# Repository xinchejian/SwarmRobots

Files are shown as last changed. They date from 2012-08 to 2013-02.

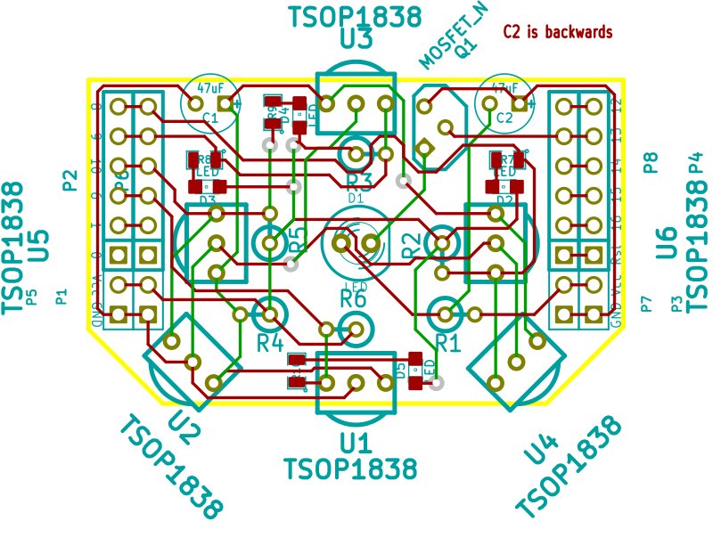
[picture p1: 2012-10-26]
AtTiny2313/hardware/swarmIRShield/swarmIR-brd.jpg

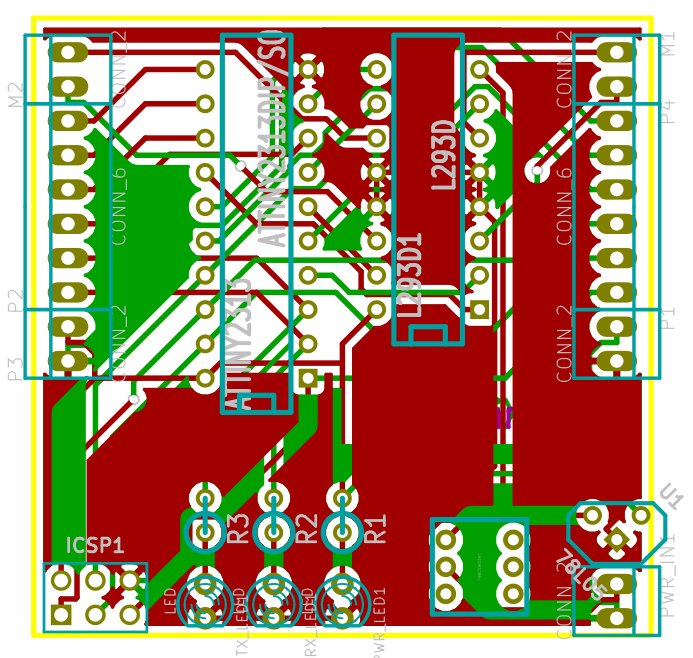
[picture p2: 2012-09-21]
AtTiny2313/hardware/mainPCB/swarmrobot-brd.jpg

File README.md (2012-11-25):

xcj_swarm
=========

Xinchejian Swarm Robot project

Introduction:

Build a swarm of robots with autonomus behavior to achieve their goals by interacting with each other using IR communication.

See each xinCheJian wiki for assembly instructions and information.

Original Requirements:
  Each basic robot contains the following:
	- 1x microcontroller Attiny2313
	- 1x motor controller L293D
	- 2x gear motors
	- 1x LiPo battery 3.7V
	Sensor shield

A custom made PCB will be used. This PCB will be mounted into a 3D printed casing which contains the gear motors and the wheels as well the IR sensor array.

Goal is that the maximum price for the basic robot should not exceed 5US$ (without shield)

Each robot will have a basic programming and basic hardware platform. 
The basic programming is:
1. Self protection: 
	- check your battery status
	- find the charging station when battery runs low
	- avoid obstacles and other robots
	- search for power (sunlight etc.)
2. Community (swarm) needs:
	- search for building material
	- search for dead robots
	- bring dead robots to the charging station
	- help dead robots with a charger robot
	- tell others where to find power (sunlight)
	- tell others where is an obstacle or danger

Folder structure:
	/32u4-edwardrf	work in progress - check XCJ mailing list for later versions.
	/AtTiny2313	AtTiny2313 version - that won the AFRON competition
	/ATMEGA328	version based on 
	/ATMEGA168	latest super version (replaces UNO version).

	Note there is a LARGE amount of direct compatability between the code for ALL versions. Differences to note are:
		- different IO pins - see "Arduino, AtTiny, L293 and header pin mappings.ods"
		- size of memory limits size of code
		- AtTiny versions have fewer IO commands available. See http://wiki.xinchejian.com/wiki/Programming-AFRON

Branches & master
	- Please use branches to do YOUR work before committing back to the master!
	- Goal is for the master to be 'production ready' at ALL TIMES!

More at the XinCheJian website wiki.xinchejian.com 
	- the original Swarmrobot pages at http://wiki.xinchejian.com/wiki/Swarm_robots
	- collated summary and AFRON competition entry
	http://wiki.xinchejian.com/wiki/Category:AFRON_$10_Robot_Competition

	latest Swarmrobot index - entry page is now: http://wiki.xinchejian.com/wiki/Category:Swarm_Robots

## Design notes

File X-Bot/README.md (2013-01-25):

简介：
   X-Bot是一款群体机器人（Swarm Robot），让这样一群小巧的机器人来实现蚁群可以完成的任务，这就是群体机器人。它由来自新车间（xinchejian.com）创客空间成员组建的一个小组创建。该机器人是基于红外线传感而制作的，它的特点是低成本、易于实践和多功能。该机器人初级版在2012年9月 “AFRON $10 robot challenge” 上获得常规组的第二名。
   该项目有Lutz提议建立，于2012年4月启动，其目的是让成员通过实践可以学到多样的技能，并促进人之间的交流。该目的通过构建个体功能很简单，但通过它们之间的合作可以完成复杂任务的小机器人来实现，这就是Swarm Robot。
该项目在进行中，核心成员为：
   Lutz Michaelis： 德国 （发起人）
   Spencer F：澳大利亚
   Edward Jiang： 中国
   Sunny Sun ：中国
   Leo Yan ： 中国

   在这里归档是LeoYan在其基础上的进一步发展的中级版本，采用了ATMEGA328，拥有更大的创作空间，通过您的加入将会使其功能更完善，也将形成一个圈子，一起交流，一起make stuff。

版权声明：
    所有文档和硬件设计采用：CC BY-NC 3.0 CN ， see <http://creativecommons.net.cn/licenses>
    所有软件代码采用      ：GPL3.0 ，          see <http://www.gnu.org/licenses/>

# English

## Programming

* Checkout and compile the log
 * Set target to Arduino Uno
 * symlink source to SwarmRobot (required by Arduino IDE projects)
* Charge the X-Bot fully
* Configure your X-Bot ID in Swbot.Config.h
 * If you want to start _START_REMOTE_CONTROL
 * Select the behavior you want

```
  #define ROBOT_TYPE_ANT  0x10 (food hunter)
  #define ROBOT_TYPE_ANT_LINEUP 0x11 (line up to and follow the higher id)
  #define ROBOT_TYPE_FOOD 0x21 (turns your X-Bot into a edible source of food)
```
 * Verify the program (compilation step)
* Connect the USB TTL Programmer v2 to your USB
 * Align VCC to VCC
* Upload, should end up with Arduino 1.0.1:

```
avrdude done.  Thank you.
```

## Details

## Behavior changes

In Action.cpp, behavior is defined in RuleTbl as a state machine.

Below, an example using the food hunter behavior:

This represents the current state and the action to do (internal state):

    {INTERIORINFO, TASK_STAGE, TS_LOOKING,  0, 0, 0,  true},

The action is activated under each state by ANYINFO:

    {ANYINFO, 0, 0,  ACTION_IN_SET, TASK_STAGE, TS_LOOKING,  false },

(last boolean is used to create a linked-list of actions to be done following a state)

The first 3 parameters define the conditional for an action... In the case of ANYINFO, there's no conditional so parameters are zero:

    {ANYINFO, 0, 0,  ACTION_EXT_LED, LED_MODE_MANUAL, 0B00,  true},

If the type of message is FOOD, the action is to set the internal variable target to true and keep target id

    {ROBOTINFO_TYPE, ROBOT_ID_ANY, ROBOT_TYPE_FOOD,  ACTION_IN_SET, TARGET, INFO_STATE_SET,  true},

If the TARGET variable is set, then change the state to TS_FOUND:

    {INTERIORINFO, TARGET, INFO_STATE_SET,  ACTION_IN_SET, TASK_STAGE, TS_FOUND,  false},

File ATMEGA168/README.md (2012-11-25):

xcj_swarm
=========

Xinchejian Swarm Robot project

This folder is for the Arduino atmega168 based SwarmRobot version.

It is the most advanced hardware and software SwarmRobot as at November 2012!

Folder structure:
	/hardware	- Eagle v6 schematic and PCB files
	/source 	- all the source code - can edit/compile in Arduino GUI!

Contact: leo.yan.cn@gmail.com

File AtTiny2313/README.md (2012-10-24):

xcj_swarm/AtTiny2313
=========

Part of Xinchejian Swarm Robot project - contains ALL software and hardware for AtTiny2313 SwarmRobots.

As there are now many different types of SwarmRobots, moving all AtTiny2313 files here.

hardware/swarmIRShield			Shield for IR follow/avoid, object detection and communications
hardware/mainPCB			Main processor & motor controller

software/IR_Follow			IR follow has bugs not working very well
software/IR_Follow_AFRON		IR follow released for AFRON competition + has bug fix
software/IR_object_detection		IR object detection
software/SwitchShield_Avoid_Follow  	Wall avoid or follow using micro-switch shield (only on proto-board - no PCB done yet!)
/software/SwarmIRControl		SwarmRobot(s) respond to RC5 IR comamnds
					Build from command line 'make' - so you need a compiler setup!
/software/SwarmIRControllerArduino	Send RC5 commands to SwarmRobot(s) using an Arduino 
						(most remotes in China are NEC protocol!)
/software/Swarm_Random_Demo		SwarmRobot moves in random direction for random time (6 seconds max) 
						- no shield required!

... to do for software/SwarmIRControl
	- add non-rc5 ie any IR follow to SwarmIRControl
	- more doco on compiling & settting up compiler....
		(if you have Arduino installed - you should have it already, maybe need path..)

************************************************************
Changes made to move from previous mess to this structure:-

/swarmIR		-> AtTiny2313/hardware/swarmIRShield
/kicad			-> AtTiny2313/hardware/mainPCB

/source-Avoid-Follow	-> AtTiny2313/software/SwitchShield_Avoid_Follow 
/source-IR		-> AtTiny2313/software/IR_Follow_AFRON
/swarm_wall_follow_ir	-> AtTiny2313/software/IR_object_detection

All the Arduino code files also renamed so can open sketches in the folder!

************************************************************

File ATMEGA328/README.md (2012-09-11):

xcj_swarm
=========

Xinchejian Swarm Robot project

This folder is for the custom PCB ATMEGA328 SwarmRobot version.

Folder structure:

	/eagle 		kicad schematics and PCB design files
	/source		source code

	Note there is a LARGE amount of direct compatability between the code for ALL versions. Differences to note are:
		- different IO pins - see "Arduino, AtTiny, L293 and header pin mappings.ods"
		- size of memory limits size of code
		- AtTiny versions have fewer IO commands available. See http://wiki.xinchejian.com/wiki/Programming-AFRON

More at the XinCheJian website wiki.xinchejian.com 
	- the original Swarmrobot pages at http://wiki.xinchejian.com/wiki/Swarm_robots
	- collated summary and AFRON competition entry
		 - URL not yet published, but after 15/9/2012 you will find it via 
				http://wiki.xinchejian.com/wiki/Category:AFRON_$10_Robot_Competition

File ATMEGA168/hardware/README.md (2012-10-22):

xcj_swarm
=========

Xinchejian Swarm Robot project

Introduction:

Build a swarm of robots with autonomus behavior to achieve their goals by interacting with each other using IR communication.

Requirements:

Each basic robot contains the following:
	
	- 1x microcontroller Attiny2313
	- 1x motor controller L293D
	- 2x gear motors
	- 1x LiPo battery 3.7V
	Sensor shield

A custom made PCB will be used. This PCB will be mounted into a 3D printed casing which contains the gear motors and the wheels as well the IR sensor array.

Goal is that the maximum price for the basic robot should not exceed 5US$ (without shield)

Each robot will have a basic programming and basic hardware platform. 
The basic programming is:

1. Self protection: 
	- check your battery status
	- find the charging station when battery runs low
	- avoid obstacles and other robots
	- search for power (sunlight etc.)
2. Community (swarm) needs:
	- search for building material
	- search for dead robots
	- bring dead robots to the charging station
	- help dead robots with a charger robot
	- tell others where to find power (sunlight)
	- tell others where is an obstacle or danger

Folder structure:

	/kicad 		AtTin2313 - kicad schematics and PCB design files
	/source		AtTin2313 - source code

	/ATMEGA328	version based on 
	/UNO		version built onto and existing Arduino UNO.

	Note there is a LARGE amount of direct compatability between the code for ALL versions. Differences to note are:
		- different IO pins - see "Arduino, AtTiny, L293 and header pin mappings.ods"
		- size of memory limits size of code
		- AtTiny versions have fewer IO commands available. See http://wiki.xinchejian.com/wiki/Programming-AFRON

Branches & master
	- Please use branches to do YOUR work before committing back to the master!
	- Goal is for the master to be 'production ready' at ALL TIMES!

Sample Git info:
    http://kentnguyen.com/development/visualized-git-practices-for-team/
    http://gitref.org/branching/
    http://marklodato.github.com/visual-git-guide/index-en.html
    http://think-like-a-git.net/
    https://github.com/diaspora/diaspora/wiki/Git-Workflow

More at the XinCheJian website wiki.xinchejian.com 
	- the original Swarmrobot pages at http://wiki.xinchejian.com/wiki/Swarm_robots
	- collated summary and AFRON competition entry
		 - URL not yet published, but after 15/9/2012 you will find it via 
				http://wiki.xinchejian.com/wiki/Category:AFRON_$10_Robot_Competition

************************************************************
Changes made to move from previous mess to this structure:-

/swarmIR		-> AtTiny2313/hardware/swarmIRShield
/kicad			-> AtTiny2313/hardware/mainPCB

/source-Avoid-Follow	-> AtTiny2313/software/SwitchShield_Avoid_Follow 
/source-IR		-> AtTiny2313/software/IR_Follow_AFRON
/swarm_wall_follow_ir	-> AtTiny2313/software/IR_object_detection

All the Arduino code files also renamed so can open sketches in the folder!

************************************************************

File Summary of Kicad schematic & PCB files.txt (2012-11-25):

2012-11-25 This file is now just for historical use - it now lenger matches current structure!

The following is a history of Schematic & PCB files, extracted from the git commit log.

5/6/12   swarmrobot 			- Schematic & PCB

6/6/12   swarmrobot_new			- PCB ** 9/8/12 Edward & Lutz confirmed this was THE PCB that was made AND is the CURRENT PCB.
6/6/12   swarmrobot_new_route 		- routing only? (.do, dsn, log, rtr, ses, sts)

20/6/12  swarmrobot_new_reduced 	- Schematic & PCB (pdf, jpg copies added 8/8/12)
20/6/12  attiny85_board_optimized 	- PCB

?? Uncommited work in progress to reduce PCB size.

10/8/12	kicad/edward_version/swarmrobot.* edward's version of routed prototype sent for printing
			attiny85_board_optimized.*
			swarmrobot_new_route.*
			swarmrobot_new_reduced.*
			swarmrobot.*				<< Looks complete & seems to match actual PCBs made!

			/export9Aug2012
				swarmrobot.*

			/export14jul
				swarmrobot.*

			/lib

11/9/12 big tidy up prior to AFRON competition!
	- deleted all files from /kicad & commited
	- moved kicad/edward_version/swarmrobot.* & /export9Aug2012 to /kicad
	- deleted all remaining files in kicad/edward_version/
	- committed		-- if you need any of the older files, please go to the commits tab and find them!
						or try a visiual git interface like gitk
						or read something like http://rogerdudler.github.com/git-guide/

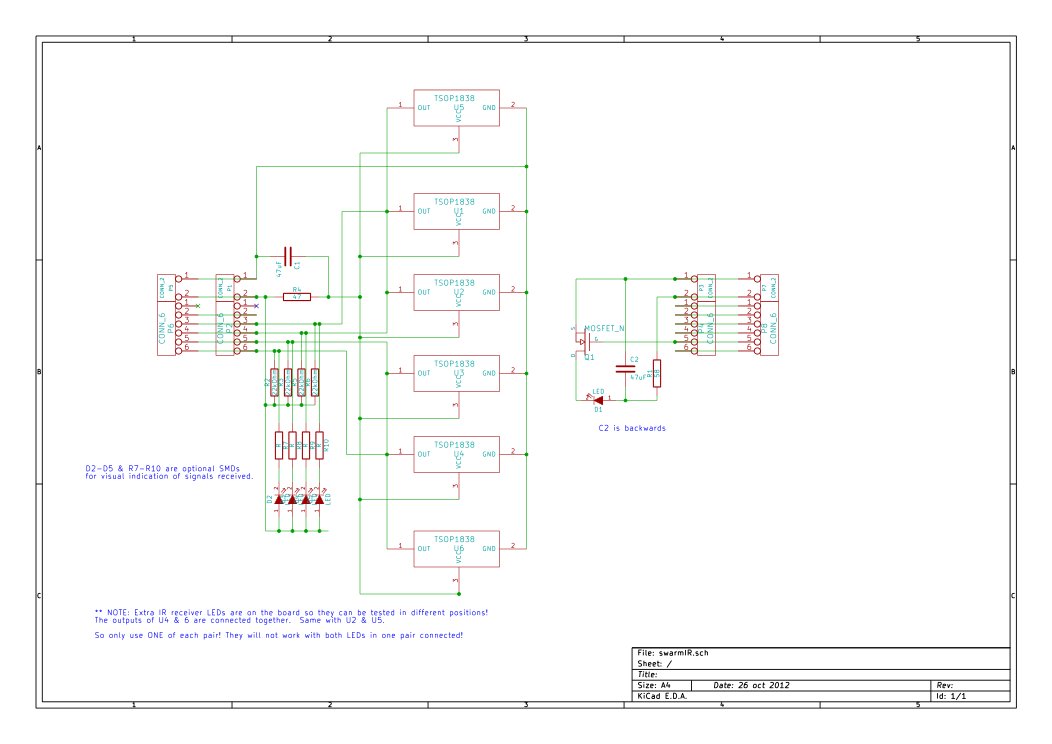
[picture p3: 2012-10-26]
AtTiny2313/hardware/swarmIRShield/swarmIR.jpg

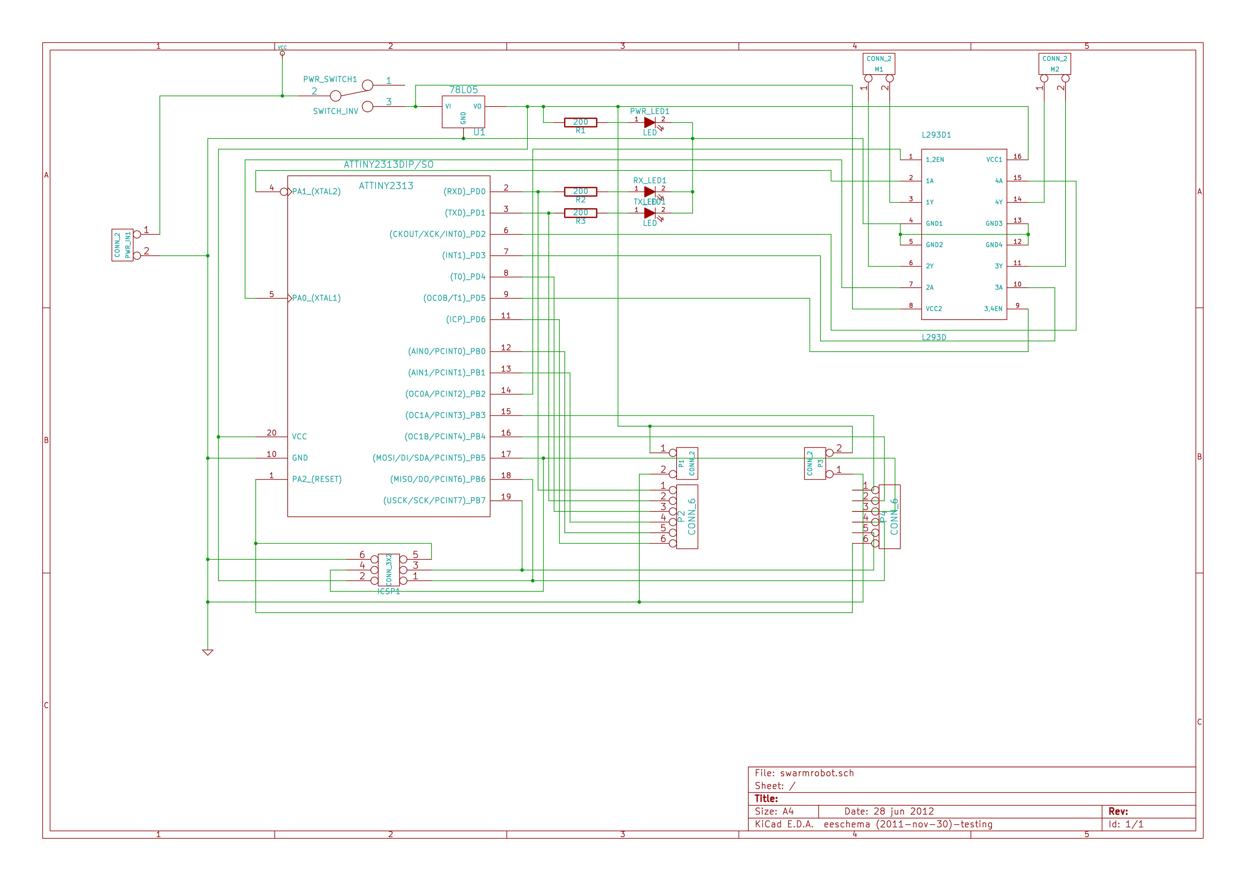
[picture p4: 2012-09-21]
AtTiny2313/hardware/mainPCB/swarmrobot.jpg

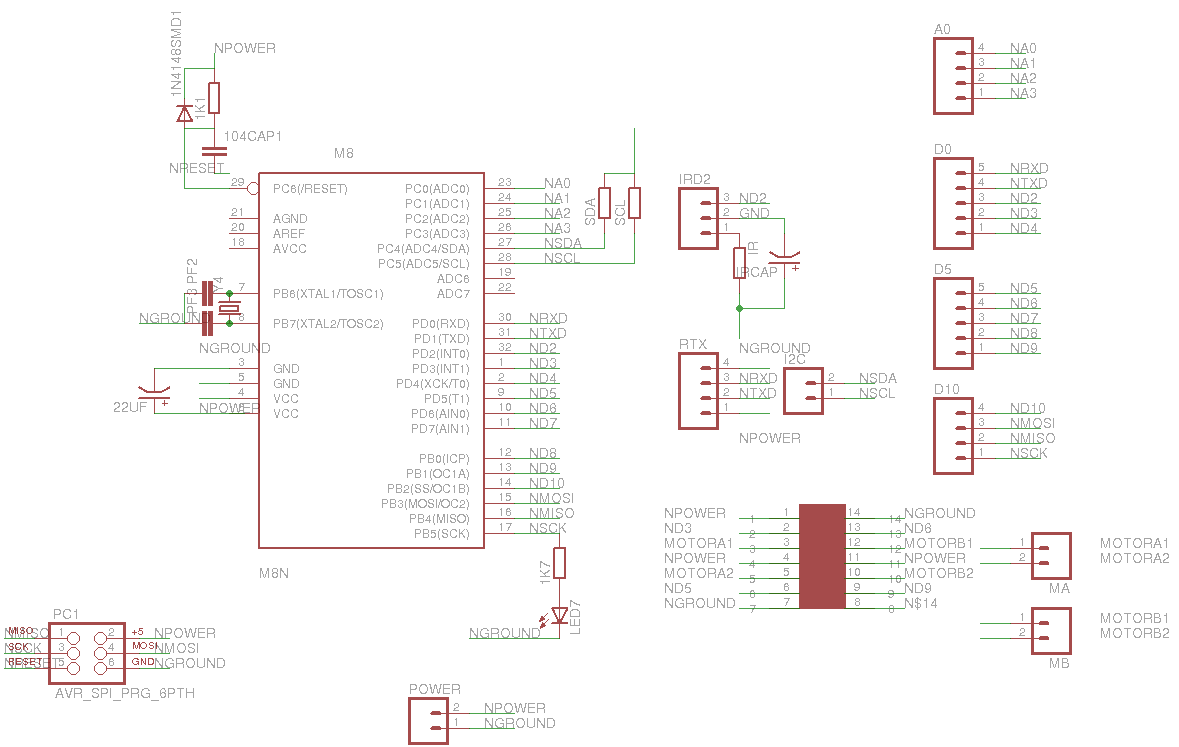
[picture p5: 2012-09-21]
ATMEGA328/eagle/pcbmotor_schematic.png

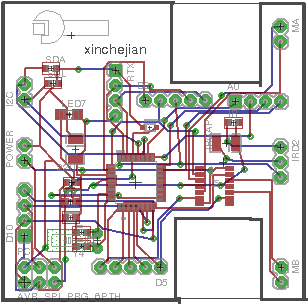
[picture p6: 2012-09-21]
ATMEGA328/eagle/pcbmotor.png

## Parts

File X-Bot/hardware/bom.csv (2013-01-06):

名称 | Item | Package | Type | Quantity
MCU | MCU | TQFP | ATMEGA328P-AU | 1
电机驱动 | MOTOR DRIVER | MFP14S | LB1836M | 1
晶振 | CRISTAL | EIA3528 (TXC-7A) | 16M | 1
大电流磁珠 | Ferrite bead | 0805 | 大电流磁珠 300R 1.5A | 2
红外发射管 | IR-LED | 5mm | IR-LED | 1
一体化红外接收管 | IR-RECEIVER | TSOP | NJL21V400A | 4
LED | LED | 0805 | green | 2
LED | LED | 0805 | orange | 4
LED | LED | 5mm | red LED 红色 | 1
排针 | Pin header | 间距2.54mm 针长12mm | 1X40 | 0.5
排针 | Pin header | 间距2.54mm 针长12mm | 2X40 | 0.1
排针 | Pin header | 间距2.54mm | 90度 1X40 | 0.2
排母 | Pin socket | 2.54mm | 1X08 | 3
排母 | Pin socket | 2.54mm | 1X12 | 2
电阻 | resistor | 0805 | 100K (1/100precision) | 1
电阻 | resistor | 0805 | 33K (1/100precision) | 1
电阻 | resistor | 0805 | 1k | 7
电阻 | resistor | 0805 | 150R | 2
电阻 | resistor | 0805 | 10K | 1
电阻 | resistor | 0805 | 47R | 4
瓷电容 | capacitor | 0805 | 0.1uF | 6
瓷电容 | capacitor | 0805 | 22p | 2
瓷电容 | capacitor | 1206 | 22uF | 5
钽电容 | tantalum capacitor | EIA3528 | 47uF | 1
带保护板锂电池 | Li Battery | Larger than 180mA | 3cmX2cm | 1
小拨动开关 | 小拨动开关 | 8mm*4mm 柄5mm | SS-12D0 | 1
Motor 微型直流减速电机 | Motor 微型直流减速电机 |  | J9xx | 2
Screw 平头螺丝 | Screw 平头螺丝 |  | M2*8 | 2
wheel 皮带轮 | wheel 皮带轮 | 橙色或白色 | 17*4*1.9 | 2
垫片 | 垫片 | O型 | inter diameter 2.5 mm | 2
O型圈密封圈 | O型圈密封圈 |  | 外径15，线径2 | 2
硬纸片 | Card board | 30mmX30mm | 比如牙膏包装盒，不透光 | 1

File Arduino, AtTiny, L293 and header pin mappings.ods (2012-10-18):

Arduino | Atmega328-P | Atmega328-AU | Attiny2313 |  |  |  |  | PCB – 30 sent to make on 2012-08-9
IO Pin# | Chip pin# | Chip pin# | pin | Use1 | Use2 | Use3 | Pin | Use 1 | Use 2
RESET | 1 | 29 | 1 | PA2 | /Reset | dW | P4 1 |  | ICSP5 Reset
D0 | 2 | 30 | 2 | PD0 | RXD |  | P2 1 | Rx
D1 | 3 | 31 | 3 | PD1 | TXD |  | P2 2 | Tx |  | L293D (care dif pinouts??)
D2 | 4 | 32 | 4 | PA1 | XTAL2 |  |  | MLF |  | 2 | In1
D3 | 5 | 1 | 5 | PA0 | XTAL1 |  |  | MLB |  | 7 | In2
D4 | 6 | 2 | 6 | PD2 | CKOUT/XCK | INT0 |  | MRF |  | 15 | In4
D5 | 11 | 9 | 7 | PD3 |  | INT1 |  | MRB |  | 10 | In3
D6 | 12 | 10 | 8 | PD4 |  | T0 | P2 3 | IR_FC
D7 | 13 | 11 | 9 | PD5 | OSCOB | T1 |  | MREn |  | 9 | En2
 |  |  | 10 | GND |  |  |  |  | ICSP6 Gnd
D8 | 14 | 12 | 11 | PD6 | ICP |  | P2 6 | IR_FL
D9 | 15 | 13 | 12 | PB0 | AIN0 | PCINT0 | P2 5 | IR_R
D10 | 16 | 14 | 13 | PB1 | AIN1 | PCINT1 | P2 4 | IR_FR
D11 | 17 | 15 | 14 | PB2 | OCOA | PCINT2 |  | MLEn |  | 1 | En1
D12 | 18 | 16 | 15 | PB3 | OC1A | PCINT3 | P4 6
D13 | 19 | 17 | 16 | PB4 | OC1B | PCINT4 | P4 5 | IR Transmit control
D14 | nc | nc | 17 | PB5 | MOSI/DI/SDA | PCINT5 | P4 4 |  | ICSP4 MOSI
D15 | nc | nc | 18 | PB6 | MISO/DO | PCINT6 | P4 3 |  | ICSP1 MISO
D16 | nc | nc | 19 | PB7 | UCSK/SCL | PCINT7 | P4 2 |  | ICSP3 UCSK or SCL?
 | nc | nc | 20 | VCC |  |  |  |  | ICSP2 Vcc
A0 | 23 | 23 | nc
A1 | 24 | 24 | nc
A2 | 25 | 25 | nc
A3 | 26 | 26 | nc
A4 | 27 | 27 | nc |  |  |  |  |  |  | This document is a work in progress – please help verify & comment on it's accuracy!
A5 | 28 | 28 | nc
A6 | nc | 19 |  |  |  | PWM pin
A7 | nc | 22 |  |  |  | Int pin
** NOTE:- the port names are DIFFERENT between AtTiny & ATMEGA chips – eg Reset is on PA2 (AtTiny2313) and PC6 (ATMEGA 328)
 |  |  | Save pins idea - the motor driver uses an enable signal, so the direction control pins can be used for other purpose while this signal is disabled!
 |  |  | Now this means the motor(s) will be OFF during this time, but the time can be short, and using PWM to drive anyway.
 |  |  | But the time do do something else can be very short – so little impact on motor/speed.
 |  |  | This would work better (have to have?) interrupt that said when chip disabled – Can get interrupts from timers – need to find out about PWM!
 |  |  | There will be BIG differences between programming this via Arduino and assembly!
 |  |  | May also be benefit in doing stuff while motors are off – eg more stable power supply (although will be rapidly recovering – ie voltage going up!) and probably more useful would be less elecrical/RF noise!
 |  |  | Another idea – with these motors/battery – do we really need to control speed – or just on/off – go/stop?
 |  |  | If so, then do not need PWM control – this might make pin choice & PCB routing easier!

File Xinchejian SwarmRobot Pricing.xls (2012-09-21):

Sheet: AtTiny2313-PTH & IR (dead bug)
Photo | Quantity | Part | Remarks | Projects | Storage Location | Available | Distributor | Link | Price per Item | Sum | Optional flag | cost | *QTY |  | US$ can save
[[File:AtTiny2313-800x.JPG|100px|thumb|left|]] | 1 | AtTiny2313-PU |  | Swarm Robot moving PCB (version 2012-08-09) | Project Shelves-r3c6-SwarmRobots | 0 | Digikey | [[http://www.digikey.com/product-detail/en/ATTINY2313A-PU/ATTINY2313A-PU-ND/2238277 link]] | 10.28 | 10.28 |  | 10.28 | 10.28
[[File:L293D-800x.JPG|100px|thumb|left]] | 1 | L293D h-Bridge Chip |  | Swarm Robot moving PCB (version 2012-08-09) | Project Shelves-r3c6-SwarmRobots | 0 | Taobao | [[http://item.taobao.com/item.htm?id=14698384627 link]] | 2.80 | 2.80 |  | 2.80 | 2.80 |  | 0.4413836
[[File:LEDs 3 colours-800x.JPG|100px|thumb|left]] | 2 | LED 3mm Red | *OPTIONAL (Front skid can be replaced with bent wire) 1xPWR_LED1 LED, 1xUsed as Front wheel/skid | Swarm Robot moving PCB (version 2012-08-09) | Project Shelves-r3c6-SwarmRobots | 0 | Taobao | [[http://item.taobao.com/item.htm?&id=10086905019 link]] | 0.00 | 0.00 | O | 0.03 | 0.06
[[File:header male DIL-800x.JPG|100px|thumb|left|]] | 1 | 3x2 2.54mm Male Dual row header (DIL) | *OPTIONAL ICSP1 CONN_3X2 | Swarm Robot moving PCB (version 2012-08-09) | Project Shelves-r3c6-SwarmRobots | 0 | Taobao | [[ link]] | 0.10 | 0.10 |  | 0.10 | 0.10 | **confirm
[[File:header male SIL closeup-800x.JPG|100px|thumb|left|]] | 1 | 2x1 2.54mm Male Single row header (SIL) | *OPTIONAL - can all be wired directly. M1, M2, PWR_IN1 | Swarm Robot moving PCB (version 2012-08-09) | Project Shelves-r3c6-SwarmRobots | 0 | Taobao | [[ link]] | 0.00 | 0.00 | O | 0.10 | 0.10 | **confirm
[[File:header female SIL x8 17-800x.JPG|100px|thumb|left|]] | 2 | 8x1 2.54mm Female Single row socket (SIL) | *OPTIONAL can wire directly | Swarm Robot moving PCB (version 2012-08-09) | Project Shelves-r3c6-SwarmRobots | 0 | Taobao | [[ link]] | 0.00 | 0.00 | O | 0.10 | 0.20 | **confirm
[[File:Switch push button PCB mount on-off-800x.JPG|100px|thumb|left|]] | 1 | SPST PCB mount | *OPTIONAL - can just plug battery in/out! PWR_SWITCH1 SWITCH_INV | Swarm Robot moving PCB (version 2012-08-09) | Project Shelves-r3c6-SwarmRobots | 0 | Taobao | [[http://item.taobao.com/item.htm?id=10841749419 link]] | 0.00 | 0.00 | O | 0.15 | 0.15
[[File:resistors 200ohm x3-800x.JPG|100px|thumb|left|]] | 3 | 200R 1/4W Resistor | *OPTIONAL R1, 2, 3 | Swarm Robot moving PCB (version 2012-08-09) | Project Shelves-r3c6-SwarmRobots | 1000 | Taobao | [[ link]] | 0.01 | 0.03 |  | 0.01 | 0.03
[[File:LEDs 3 colours-800x.JPG|100px|thumb|left]] | 1 | LED 3mm Blue | *Optional Rx | Swarm Robot moving PCB (version 2012-08-09) | Project Shelves-r3c6-SwarmRobots | 0 | Taobao | [[http://item.taobao.com/item.htm?id=10698291453 link]] | 0.00 | 0.00 | O | 0.05 | 0.05
[[File:LEDs 3 colours-800x.JPG|100px|thumb|left]] | 1 | LED 3mm Yellow | *Optional Tx | Swarm Robot moving PCB (version 2012-08-09) | Project Shelves-r3c6-SwarmRobots | 0 | Recycled - Scavenged - item | [[http://item.taobao.com/item.htm?id=10086905019 link]] | 0.00 | 0.00 | O | 0.05 | 0.05
[[File:Bottle cap wheels-800x.JPG|100px|thumb|left|]] | 2 | Wheel |  | Swarm Robot moving PCB (version 2012-08-09) | Project Shelves-r3c6-SwarmRobots | 0 | Recycled - Scavenged - item | [[ link]] | 0.00 | 0.00 | r | 0.00 | 0.00
[[File:SwarmRobot AtTiny2313 PCB.JPG|100px|thumb|left|]] | 1 | SwarmRobots PCB 2012-08-09 | *OPTIONAL - can use breadboard or deadbug wiring! | Swarm Robot moving PCB (version 2012-08-09) | Project Shelves-r3c6-SwarmRobots | 0 | Taobao | [[http://store.taobao.com/shop/view_shop.htm?user_number_id=117902299 link]] | 10.00 | 10.00 |  | 10.00 | 10.00
[[File:Motor 928-800x.JPG|100px|thumb|left|]] | 2 | Motor J928 | There many similar motors with different part numbers! | Swarm Robot moving PCB (version 2012-08-09) | Project Shelves-r3c6-SwarmRobots | 10 | Taobao | [[http://item.taobao.com/item.htm?id=13758597818 link]] | 3.00 | 6.00 |  | 3.00 | 6.00 |  | 0.945822
[[File:Screws to mount wheels-800x.JPG|100px|thumb|left|]] | 2 | screw - tiny | to attach wheels to motors | Swarm Robot moving PCB (version 2012-08-09) | Project Shelves-r3c6-SwarmRobots | 0 | Recycled - Scavenged - item | [[ link]] | 0.00 | 0.00 | r | 0.00 | 0.00
[[File:Hot melt glue.JPG|100px|thumb|left|]] | 1 | Hot melt glue | 1/20th of a stick? to attach motors and??? | Swarm Robot moving PCB (version 2012-08-09) | Project Shelves-r3c6-SwarmRobots | 0 | Taobao | [[http://item.taobao.com/item.htm?id=9604073433 link]] | 0.03 | 0.03 |  | 0.03 | 0.03
[[File:Hookup wire.JPG|100px|thumb|left|]] | 1 | Hookup wire | *OPTIONAL about 100mm for motors and maybe for battery, or use two strands of Rainbow cable | Swarm Robot moving PCB (version 2012-08-09) | Project Shelves-r3c6-SwarmRobots | 0 | Recycled - Scavenged - item | n/a | 0.00 | 0.00 | r | 0.00 | 0.00
[[File:IC socket 16pin-800x.JPG|100px|thumb|left|]] | 3 | 16pin DIP IC socket | *Optional – can solder IC directly | Swarm Robot moving PCB (version 2012-08-09), Swarm Robot moving PCB (version 2012-08-09) | Big Shelves-r2c4 | 0 | Taobao | [[http://s.taobao.com/search?q=14%D2%FD%BD%C5IC%B2%E5%D7%F9&initiative_id=staobaoz_20120909 link]] | 0.00 | 0.00 | O | 0.18 | 0.54
[[File:Battery 3.7V rechargable-800x.JPG|100px|thumb|left|]] | 1 | Lithium 180mA 3.7V |  | Swarm Robot moving PCB (version 2012-08-09) | Project Shelves-r3c6-SwarmRobots | 0 | Taobao | [[http://item.taobao.com/item.htm?id=10651345659&amp; link]] | 8.00 | 8.00 |  | 8.00 | 8.00 |  | 1.261096
[[File:battery charger USB-800x.JPG|100px|thumb|left|]] | 1 | USB lithium battery charger | *Optional - Do not need 1 for every SwarmBot | Swarm Robot moving PCB (version 2012-08-09) | Project Shelves-r3c6-SwarmRobots | 0 | Taobao | [[http://item.taobao.com/item.htm?id=10651070573&amp; link]] | 2.00 | 2.00 |  | 2.00 | 2.00 |  | 0.315274
[[File:USB ASP ISP -jump ON.JPG|100px|thumb|left|]] | 1 | ISP Programmer |  | Swarm Robot moving PCB (version 2012-08-09) | Not yet Allocated - To Be Determined TBD | 0 | Taobao | [[http://item.taobao.com/item.htm?id=16205331756 link]] | 18.00 | 18.00 |  | 18.00 | 18.00 |  | 2.837466
[[File:IC socket 20pin-800x.JPG|100px|thumb|left|]] | 1 | 20pin DIP IC socket | *Optional – can solder IC directly | Swarm Robot moving PCB (version 2012-08-09) | Big Shelves-r2c4 | 0 | Taobao | [[http://item.taobao.com/item.htm?id=5472654366 link]] | 0.00 | 0.00 | O | 0.11 | 0.11
[[File:1838B IR receiver LED x4-800x.JPG|100px|thumb|left|]] | 4 | 1838B or TSOP1838B or VS1838B |  | Swarm Robot IR Shield - prototype 2 - matches moving PCB version 2012-08-09 | Project Shelves-r3c6-SwarmRobots | 0 | Taobao | [[http://item.taobao.com/item.htm?id=14691731276 link]] | 0.45 | 1.80 |  | 0.45 | 1.80
[[File:Hookup wire.JPG|100px|thumb|left|]] | 1 | Hookup wire | about 100-200mm, more if LEDs used | Swarm Robot IR Shield - prototype 2 - matches moving PCB version 2012-08-09 | Project Shelves-r3c6-SwarmRobots | 0 | Recycled - Scavenged - item | n/a | 0.00 | 0.00 | r | 0.00 | 0.00
[[File:Remote control.JPG|100px|thumb|left|]] | 1 | Remote control | *OPTIONAL - use 1 for each LED | Swarm Robot IR Shield - prototype 2 - matches moving PCB version 2012-08-09 |  |  | Recycled - Scavenged - item | n/a | 0.00 | 0.00 |  | 0.00 | 0.00
 |  |  |  |  |  |  |  |  | TOTAL Y | 59.04 | 1.26 |  | 60.30 |  | 5.8010416
These parts are for the complete main/base PCB AND four IR receiver LEDs connected “dead bug” style |  |  |  |  |  |  |  |  | Total US$ | 9.30638012 | 0.19862262 |  | 9.50500274 |  | Red = can scavenge, but has been included!
 |  |  |  |  |  |  |  | less the RED items |  | 3.50533852 |  |  | 3.70396114
 |  |  |  |  |  |  |  | xe.com exchange rate on 9/9/12 |  |  | 0.157637 | RMB per US dollar
 |  |  |  |  |  |  |  | Cost of the IR Senors |  | 0.2837466

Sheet: AtTiny2313-PTH IR Shield
Photo |  | Quantity | Part | Remarks | Projects | Storage Location | Available | Distributor | Link | Price per Item | Sum | Optional flag | cost | *QTY |  | US$ can save
[[File:1838B IR receiver LED x4-800x.JPG|100px|thumb|left|]] |  | 4 | 1838B or TSOP1838B or VS1838B |  | Swarm Robot IR Shield - prototype 2 - matches moving PCB version 2012-08-09 | Project Shelves-r3c6-SwarmRobots | 0 | Taobao | [[http://item.taobao.com/item.htm?id=14691731276 link]] | 0.45 | 1.80 |  | 0.45 | 1.80
[[File:Shield Breadboard-800x.JPG|100px|thumb|left|]] |  | 1 | PCB for shield |  | Swarm Robot IR Shield - prototype 2 - matches moving PCB version 2012-08-09 | Project Shelves-r3c6-SwarmRobots | 0 | Taobao | [[http://store.taobao.com/shop/view_shop.htm?user_number_id=117902299 link]] | 0.00 | 0.00 | O | 10.00 | 10.00 | **confirm
[[File:header male SIL closeup-800x.JPG|100px|thumb|left|]] |  | 2 | 8x1 2.54mm Male Single row header (SIL) |  | Swarm Robot IR Shield - prototype 2 - matches moving PCB version 2012-08-09 | Project Shelves-r3c6-SwarmRobots | 0 | Taobao | [[ link]] | 0.10 | 0.20 |  | 0.10 | 0.20
[[File:Hookup wire.JPG|100px|thumb|left|]] |  | 1 | Hookup wire | about 100-200mm, more if LEDs used | Swarm Robot IR Shield - prototype 2 - matches moving PCB version 2012-08-09 | Project Shelves-r3c6-SwarmRobots | 0 | Recycled - Scavenged - item | n/a | 0.00 | 0.00 | r | 0.00 | 0.00
[[File:LEDs 3 colours-800x.JPG|100px|thumb|left]] |  | 4 | LED 3mm 4 colours | *OPTIONAL - just flashy/showy/debug! | Swarm Robot IR Shield - prototype 2 - matches moving PCB version 2012-08-09 | Project Shelves-r3c6-SwarmRobots | 0 | Taobao | [[http://item.taobao.com/item.htm?id=10698291453 link]] | 0.00 | 0.00 | O | 0.05 | 0.20
[[File:Resistors 150 ohm.JPG|100px|thumb|left|]] |  | 4 | 150R 1/4W Resistor | *OPTIONAL - use 1 for each LED | Swarm Robot IR Shield - prototype 2 - matches moving PCB version 2012-08-09 | ResistorWallRack1 | 1 | Taobao | [[ link]] |  | 0.00 | O | 0.01 | 0.04
[[File:Remote control.JPG|100px|thumb|left|]] |  | 1 | Remote control | *OPTIONAL - use 1 for each LED | Swarm Robot IR Shield - prototype 2 - matches moving PCB version 2012-08-09 |  |  | Recycled - Scavenged - item | n/a | 0.00 | 0.00 |  | 0.00 | 0.00
[[File:IR333A IR led.JPG|100px|thumb|left|]] |  | 1 | IR333A IR led | for IR distance | Swarm Robot IR Shield - prototype 2 - matches moving PCB version 2012-08-09 |  |  | Taobao | [[http://item.taobao.com/item.htm?id=15629283525 link]] | 0.00 | 0.00 |  | 0.15 | 0.15
[[File:2n7000 n-FET IR led.JPG|100px|thumb|left|]] |  | 1 | 2n7000 n-FET | for IR distance | Swarm Robot IR Shield - prototype 2 - matches moving PCB version 2012-08-09 |  |  | Taobao | [[http://item.taobao.com/item.htm?id=10067854980 link]] | 0.00 | 0.00 |  | 0.18 | 0.18
[[File:Resistors 150 ohm.JPG|100px|thumb|left|]] |  | 1 | 50 Ohm resistor | for IR distance | Swarm Robot IR Shield - prototype 2 - matches moving PCB version 2012-08-09 |  |  | Taobao | [[ link]] | 0.00 | 0.00 |  | 0.01 | 0.01
 |  | 1 | Aluminium foil | small pieces to shield the IR LEDs |  |  |  | Recycled - Scavenged - item |  | 0.00 | 0.00 |  | 0.00 | 0.00
 |  | 1 | delivery fees |  |  |  |  |  |  | 6.00 | 6.00 |  | 12.00 | 12.00
 |  |  |  |  |  |  |  |  |  | TOTAL Y | 8.00 |  |  | 24.58 |  | 0
 |  |  |  |  | xe.com exchange rate on 9/9/12 |  |  | 0.157637 |  | Total US$ | 1.261096 |  |  | 3.87471746 |  | Red = can scavenge, but has been included!
 | These parts are ONLY for the simple IR receiver shield and optionally the distance measuring IR |  |  |  |  |  |  |  | less the RED items |  | 1.261096 |  |  | 3.87471746
 |  |  |  |  |  |  |  |  |  |  |  |  | RMB per US dollar

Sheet: Mechanical-Object-avoid-Shield
Photo | Quantity | Part | Remarks | Distributor | Distributor Order Number | Price per Item | Sum
[[File:Shield Breadboard-800x.JPG|100px|thumb|left|]] | 1 | Breadboard 3x7cm | Size is important so that switches 'reach' out and touch objects! | Taobao | [[http://item.taobao.com/item.htm?id=10520820340 link]] | 0.8 | 0.8
[[File:header male SIL closeup-800x.JPG|100px|thumb|left|]] | 2 | 8x1 2.54mm Male Single row header (SIL) |  | Taobao | [[ link]] | 0.1 | 0.2
[[File:Hookup wire.JPG|100px|thumb|left|]] | 1 | Hookup wire |  | Recycled - Scavenged - item |  | 0 | 0
[[File:MicroSwitch.JPG|100px|thumb|left|]] | 3 | Micro Switch SS-5GL2 | any one with lever or roller will do (or can add a 'whisker extension' for example a plastic tube/strip) | Taobao | [[http://item.taobao.com/item.htm?id=15056293691 link]] | 1.4 | 4.2
 | 2 | delivery fees |  | Taobao |  | 6 | 12
 |  |  |  |  |  | TOTAL Y | 17.2
 |  |  |  |  |  | Total US$ | 2.71
 |  |  |  |  | xe.com exchange rate on 9/9/12 |  |  | 0.157637

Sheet: AtTiny2313-SMD
Project | Quantity | Part | Remarks | Projects | Storage Location | Available | Distributor | Distributor Order Number | Price per Item | Sum | Optional flag | cost | *QTY | NOTES | US$ can save | SMD
Main PCB | 1 | AtTiny2313 |  | Swarm Robot moving PCB (version 2012-08-09) | Project Shelves-r3c6-SwarmRobots | 0 | Taobao | http://item.taobao.com/item.htm?id=15799462087 | 5.5 | 5.5 |  | 5.5 | 5.5 |  |  | SMD
Main PCB | 1 | L293D h-Bridge Chip |  | Swarm Robot moving PCB (version 2012-08-09) | Project Shelves-r3c6-SwarmRobots | 0 | Taobao | http://item.taobao.com/item.htm?id=13407786821 | 2.5 | 2.5 |  | 2.5 | 2.5 |  | 0.3940925 | SMD
Main PCB | 2 | LED 3mm Red | Swarm Robot moving PCB (version 2012-08-09): *OPTIONAL (Front skid can be replaced with bent wire) 1xPWR_LED1 LED, 1xUsed as Front wheel/skid | Swarm Robot moving PCB (version 2012-08-09) | Project Shelves-r3c6-SwarmRobots | 0 | Optional - use for optional parts in a project! Set price to 0.001 if you want teh supplier to appear in project report! | http://item.taobao.com/item.htm?id=6842780895 | 0 | 0 | O | 0.06 | 0.12 |  |  | SMD
Main PCB | 1 | 3x2 2.54mm Male Dual row header (DIL) | Swarm Robot moving PCB (version 2012-08-09): *OPTIONAL ICSP1 CONN_3X2 | Swarm Robot moving PCB (version 2012-08-09) | Project Shelves-r3c6-SwarmRobots | 0 | Taobao |  | 0.1 | 0.1 |  | 0.1 | 0.1 | **confirm
Main PCB | 1 | 2x1 2.54mm Male Single row header (SIL) | Swarm Robot moving PCB (version 2012-08-09): *OPTIONAL - can all be wired directly. M1, M2, PWR_IN1 | Swarm Robot moving PCB (version 2012-08-09) | Project Shelves-r3c6-SwarmRobots | 0 | Optional - use for optional parts in a project! Set price to 0.001 if you want teh supplier to appear in project report! |  | 0 | 0 | O | 0.1 | 0.1 | **confirm
Main PCB | 2 | 8x1 2.54mm Female Single row socket (SIL) | Swarm Robot moving PCB (version 2012-08-09): *OPTIONAL can wire directly | Swarm Robot moving PCB (version 2012-08-09) | Project Shelves-r3c6-SwarmRobots | 0 | Optional - use for optional parts in a project! Set price to 0.001 if you want teh supplier to appear in project report! |  | 0 | 0 | O | 0.1 | 0.2 | **confirm
Main PCB | 1 | SPST PCB mount | Swarm Robot moving PCB (version 2012-08-09): *OPTIONAL - can just plug battery in/out! PWR_SWITCH1 SWITCH_INV | Swarm Robot moving PCB (version 2012-08-09) | Project Shelves-r3c6-SwarmRobots | 0 | Optional - use for optional parts in a project! Set price to 0.001 if you want teh supplier to appear in project report! | http://item.taobao.com/item.htm?id=10841749419 | 0 | 0 | O | 0.15 | 0.15
Main PCB | 3 | 200R 1/4W Resistor | Swarm Robot moving PCB (version 2012-08-09): *OPTIONAL (Front skid can be replaced with bent wire) 1xPWR_LED1 LED, 1xUsed as Front wheel/skid | Swarm Robot moving PCB (version 2012-08-09) | Project Shelves-r3c6-SwarmRobots | 0 | Optional - use for optional parts in a project! Set price to 0.001 if you want teh supplier to appear in project report! |  | 0 | 0 | O | 0.01 | 0.03 |  |  | SMD
Main PCB | 1 | LED 3mm Blue | Swarm Robot moving PCB (version 2012-08-09): *Optional Rx | Swarm Robot moving PCB (version 2012-08-09) | Project Shelves-r3c6-SwarmRobots | 0 | Optional - use for optional parts in a project! Set price to 0.001 if you want teh supplier to appear in project report! | http://item.taobao.com/item.htm?id=6842780895 | 0 | 0 | O | 0.06 | 0.06 |  |  | SMD
Main PCB | 1 | LED 3mm Yellow | Swarm Robot moving PCB (version 2012-08-09): *Optional Rx | Swarm Robot moving PCB (version 2012-08-09) | Project Shelves-r3c6-SwarmRobots | 0 | Optional - use for optional parts in a project! Set price to 0.001 if you want teh supplier to appear in project report! | http://item.taobao.com/item.htm?id=6842780895 | 0 | 0 | O | 0.06 | 0.06 |  |  | SMD
Main PCB | 2 | Wheel |  | Swarm Robot moving PCB (version 2012-08-09) | Project Shelves-r3c6-SwarmRobots | 0 | Recycled - Scavenged - item |  | 0 | 0 | r | 0 | 0
Main PCB | 1 | SwarmRobots PCB 2012-08-09 | Swarm Robot moving PCB (version 2012-08-09): *OPTIONAL - can use breadboard or deadbug wiring! | Swarm Robot moving PCB (version 2012-08-09) | Project Shelves-r3c6-SwarmRobots | 0 | Taobao | http://store.taobao.com/shop/view_shop.htm?user_number_id=117902299 | 10 | 10 |  | 10 | 10
Main PCB | 2 | Motor J928 |  | Swarm Robot moving PCB (version 2012-08-09) | Project Shelves-r3c6-SwarmRobots | 10 | Taobao | http://item.taobao.com/item.htm?id=13758597818 | 3 | 6 |  | 3 | 6 |  | 0.945822
Main PCB | 2 | screw - tiny | Swarm Robot moving PCB (version 2012-08-09): to attach wheels to motors | Swarm Robot moving PCB (version 2012-08-09) | Project Shelves-r3c6-SwarmRobots | 0 | Recycled - Scavenged - item |  | 0 | 0 | r | 0 | 0
Main PCB | 1 | Hot melt glue | Swarm Robot moving PCB (version 2012-08-09): 1/20th of a stick? to attach motors and??? | Swarm Robot moving PCB (version 2012-08-09) | Project Shelves-r3c6-SwarmRobots | 0 | Taobao | http://item.taobao.com/item.htm?id=9604073433 | 0.03 | 0.03 |  | 0.03 | 0.03
Main PCB | 1 | Hookup wire | Swarm Robot moving PCB (version 2012-08-09): *OPTIONAL about 100mm for motors and maybe for battery, or use two strands of Rainbow cable | Swarm Robot moving PCB (version 2012-08-09) | Project Shelves-r3c6-SwarmRobots | 0 | Recycled - Scavenged - item |  | 0 | 0 | r | 0 | 0
Main PCB | 1 | Lithium 180mA 3.7V |  | Swarm Robot moving PCB (version 2012-08-09) | Project Shelves-r3c6-SwarmRobots | 0 | Taobao | http://item.taobao.com/item.htm?id=10651345659&amp; | 8 | 8 |  | 8 | 8 |  | 1.261096
Main PCB | 1 | USB lithium battery charger | Swarm Robot moving PCB (version 2012-08-09): *Optional - Do not need 1 for every SwarmBot | Swarm Robot moving PCB (version 2012-08-09) | Project Shelves-r3c6-SwarmRobots | 0 | Taobao | http://item.taobao.com/item.htm?id=10651070573&amp; | 2 | 2 |  | 2 | 2 |  | 0.315274
Main PCB | 1 | ISP Programmer |  | Swarm Robot moving PCB (version 2012-08-09) | Not yet Allocated - To Be Determined TBD | 0 | Taobao | http://item.taobao.com/item.htm?id=16205331756 | 18 | 18 |  | 18 | 18 |  | 2.837466
IR Shield | 4 | 1838B or TSOP1838B or VS1838B |  | Swarm Robot IR Shield - prototype 2 - matches moving PCB version 2012-08-09 | Project Shelves-r3c6-SwarmRobots | 0 | Taobao | http://item.taobao.com/item.htm?id=14691731276 | 0.45 | 1.8 |  | 0.45 | 1.8
IR Shield | 1 | Remote control | Swarm Robot IR Shield - prototype 2 - matches moving PCB version 2012-08-09: *OPTIONAL - use 1 for each LED | Swarm Robot IR Shield - prototype 2 - matches moving PCB version 2012-08-09 |  |  | Recycled - Scavenged - item |  | 0 | 0 |  | 0 | 0
 |  |  |  |  |  |  |  |  | TOTAL Y | 53.93 | 0.72 |  | 54.65 |  | 5.7537505
 |  |  |  |  |  |  |  |  | Total US$ | 8.50136341 | 0.11349864 |  | 8.61486205 |  | Red = can scavenge, but has been included!
 |  |  |  |  |  |  |  | less the RED items |  | 2.74761291 |  |  | 2.86111155
 |  |  |  |  |  |  |  | xe.com exchange rate on 9/9/12 |  |  | 0.157637 | RMB per US dollar

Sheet: Atmega328
this sheet is to work out cost of Sunny's ATMEGA328 SMD version!
10 rmb atmega 328p
atmega8 4rmb if we are not using pwm to control the motors ,
lb1836 1 or 2 rmb
crystal hc26 0.3
smd led 0.2
capacitor is around 0.4
http://store.taobao.com/shop/view_shop.htm?spm=a1z09.2.9.5.67e845&user_number_id=117902299
PCB 100 pieces less than 300 rmb at the current size
more compact , board price should be able to contain in 2rmb\ pcs

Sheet: PCBA Attiny
 |  | One off parts pricing shown includes ALL parts, battery & charger and programmer, except the wheels and screws.
 |  | The one-off parts prices are shown for reference only.
Estimates for a PTH version: |  |  |  |  |  |  |  | Estimates for a SMD version:
 | PTH | cost | SMD | cost |  |  |  |  | PTH | cost | SMD | cost
 | Number | estimate | solder | estimate |  |  |  |  | Number | estimate | solder | estimate
 | holes | per hole | points | per point | Totals: |  |  |  | holes | per hole | points | per point | Totals:
Soldering cost | 125 | 0.03 | 0 | 0.0075 | 0.59113875 | cost per board |  | Soldering cost | 55 | 0.03 | 64 | 0.0075 | 0.74010105 | cost per board
Fixed setup cost |  |  |  |  | 78.8185 | fixed cost |  | Fixed setup cost |  |  |  |  | 78.8185 | fixed cost
 | Includes IR shield! |  |  |  |  |  |  |  | Includes on board IR LEDs
 | QTY |  |  |  |  |  |  |  | QTY
PCBA cost per board | 1 | 100 | 1000 |  |  |  |  | PCBA cost per board | 1 | 100 | 1000
 | na | 1.37932375 | 0.66995725 |  |  |  |  |  | na | 1.52828605 | 0.81891955
 | QTY |  |  |  |  |  |  |  | QTY
Parts & PCB cost/board | 1 | 100 | 1000 |  |  |  |  | Parts & PCB cost/board | 1 | 100 | 1000
 | 9.50500274 | 5.303729786 | 4.886964058 | Note 1. |  |  |  |  | 8.61486205 | 4.807037063 | 4.429301322 | Note 1.
 | QTY |  |  |  |  |  |  |  | QTY
 | 1 | 100 | 1000 |  |  |  |  |  | 1 | 100 | 1000
Total cost/board: | na | 6.683053536 | 5.556921308 |  |  |  |  | Total cost/board: | na | 6.335323113 | 5.248220872
All the PCBA costs are based on estimates received from Taoboa shop used by several Xinchejian members for PCB supply.
No provision for any wages/costs associated with the effort of sourcing components and managing a PCBA process have been included, only the estimated cost of parts and PCBA services.
 |  |  |  |  | xe.com exchange rate on 9/9/12 |  |  | 0.157637 | RMB per US dollar
1. Discounts based on: | Volume Pricebreaks: A Double-Edged Sword for Smaller Organizations?
 | http://octopart.com/blog/archives/2011/9/volume-pricebreaks%253A-a-double%252Dedged-sword-for-smaller-organizations%253F
 |  |  |  |  |  |  | Base cost = per unit cost at specified quantity!
 |  |  |  |  | Quantity | Total Cost | Base Cost | % Discount
 |  |  |  |  | 1 | $30.79 | $30.79 | 0 |  |  |  | Note 2: Assume a typical 10% cost reduction for purchse of 10.
 |  |  |  |  | 10 | $277.10 | $27.71 | 10.00%
 |  |  |  |  | 100 | $1718.00 | $17.18 | 44.20%
 |  |  |  |  | 175 | $2929.50 | $16.74 | 45.63%
 |  |  |  |  | 500 | $7975.00 | $15.95 | 48.20%
 |  |  |  |  | 1000 | $15830.00 | $15.83 | 48.59%
 |  |  |  |  | 5000 | $76750.00 | $15.35 | 50.14%
 |  |  |  |  | 10000 | $153000.00 | $15.30 | 50.31%

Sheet: PCBA - Atmega328
 |  | One off parts pricing shown includes ALL parts, battery & charger and programmer, except the wheels and screws.
 |  | The one-off parts prices are shown for reference only.
Estimates for a PTH version: |  |  |  |  |  |  |  | Estimates for a SMD version:
 | PTH | cost | SMD | cost |  |  |  |  | PTH | cost | SMD | cost
 | Number | estimate | solder | estimate |  |  |  |  | Number | estimate | solder | estimate
 | holes | per hole | points | per point | Totals: |  |  |  | holes | per hole | points | per point | Totals:
Soldering cost | 0 | 0.03 | 0 | 0.0075 | 0 | cost per board |  | Soldering cost | 55 | 0.03 | 64 | 0.0075 | 0.74010105 | cost per board
Fixed setup cost |  |  |  |  | 78.8185 | fixed cost |  | Fixed setup cost |  |  |  |  | 78.8185 | fixed cost
 | QTY |  |  |  |  |  |  |  | QTY
PCBA cost per board | 1 | 100 | 1000 |  |  |  |  | PCBA cost per board | 1 | 100 | 1000
 | na | 0.788185 | 0.0788185 |  |  |  |  |  | na | 1.52828605 | 0.81891955
 | QTY |  |  |  |  |  |  |  | QTY
Parts & PCB cost/board | 1 | 100 | 1000 |  |  |  |  | Parts & PCB cost/board | 1 | 100 | 1000
 | 0.04 | 0.04 | 0.03685681024 | Note 1. |  |  |  |  |  | 0 | 0 | Note 1.
 |  |  |  | this sheet is to work out cost of Sunny's ATMEGA328 SMD version!
 | QTY |  |  |  |  |  |  |  | QTY
 | 1 | 100 | 1000 |  |  |  |  |  | 1 | 100 | 1000
Total cost/board: | na | 0.828185 | 0.1156753102 |  |  |  |  | Total cost/board: | na | 1.52828605 | 0.81891955
All the PCBA costs are based on estimates received from Taoboa shop used by several Xinchejian members for PCB supply.
No provision for any wages/costs associated with the effort of sourcing components and managing a PCBA process have been included, only the estimated cost of parts and PCBA services.
 |  |  |  |  | xe.com exchange rate on 9/9/12 |  |  | 0.157637 | RMB per US dollar
1. Discounts based on: | Volume Pricebreaks: A Double-Edged Sword for Smaller Organizations?
 | http://octopart.com/blog/archives/2011/9/volume-pricebreaks%253A-a-double%252Dedged-sword-for-smaller-organizations%253F
 |  |  |  |  |  |  | Base cost = per unit cost at specified quantity!
 |  |  |  |  | Quantity | Total Cost | Base Cost | % Discount
 |  |  |  |  | 1 | $30.79 | $30.79 | 0 |  |  |  | Note 2: Assume a typical 10% cost reduction for purchse of 10.
 |  |  |  |  | 10 | $277.10 | $27.71 | -61.29%
 |  |  |  |  | 100 | $1718.00 | $17.18 | 0.00%
 |  |  |  |  | 175 | $2929.50 | $16.74 | 2.56%
 |  |  |  |  | 500 | $7975.00 | $15.95 | 7.16%
 |  |  |  |  | 1000 | $15830.00 | $15.83 | 7.86%
 |  |  |  |  | 5000 | $76750.00 | $15.35 | 10.65%
 |  |  |  |  | 10000 | $153000.00 | $15.30 | 10.94%

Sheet: Wiki export info
 | Total |  | cost
 | PTH |  | SMD
All part | $US | 9.51 | $US | 8.61
Without optional parts | $US | 9.31 | n/a
Advanced config: | $US | 3.51 | n/a |  | - see below for Sharing of parts and salvaging

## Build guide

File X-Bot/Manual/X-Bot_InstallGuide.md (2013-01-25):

V2.1:   https://skydrive.live.com/redir?resid=2B9CFF6D7DE5D891!106&authkey=!APcqGdOVx675RZY

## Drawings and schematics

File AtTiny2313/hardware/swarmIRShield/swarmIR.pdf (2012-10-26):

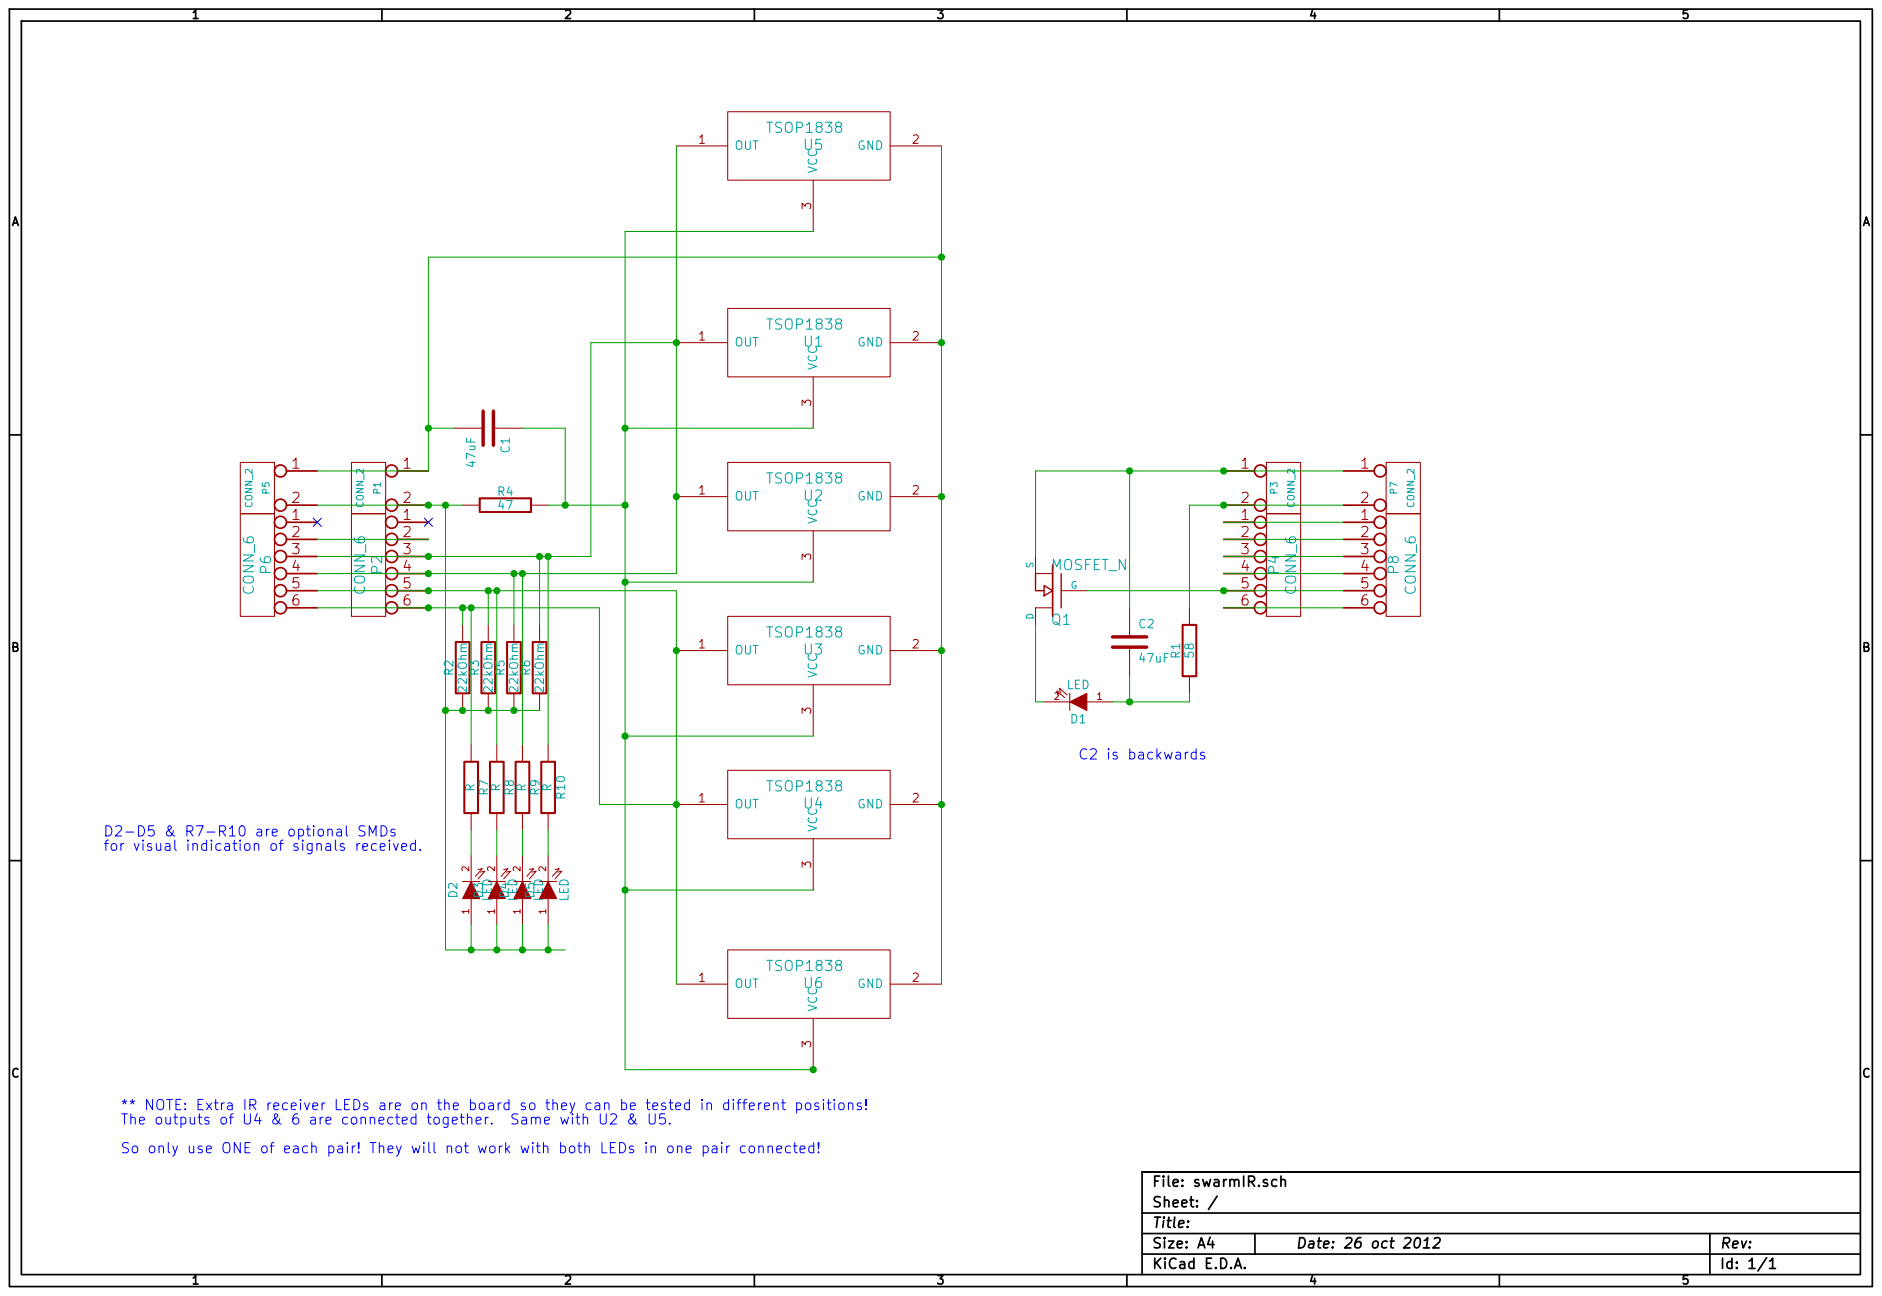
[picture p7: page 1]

D2-D5 & R7-R10 are optional SMDs
for visual indication of signals received.

1 2 D2 LED 1 2 D3 LED 1 2 D4 LED 1 2 D5 LED

** NOTE: Extra IR receiver LEDs are on the board so they can be tested in different positions!
So only use ONE of each pair! They will not work with both LEDs in one pair connected!

Id: 1/1 Title: File: swarmIR.sch Sheet: /

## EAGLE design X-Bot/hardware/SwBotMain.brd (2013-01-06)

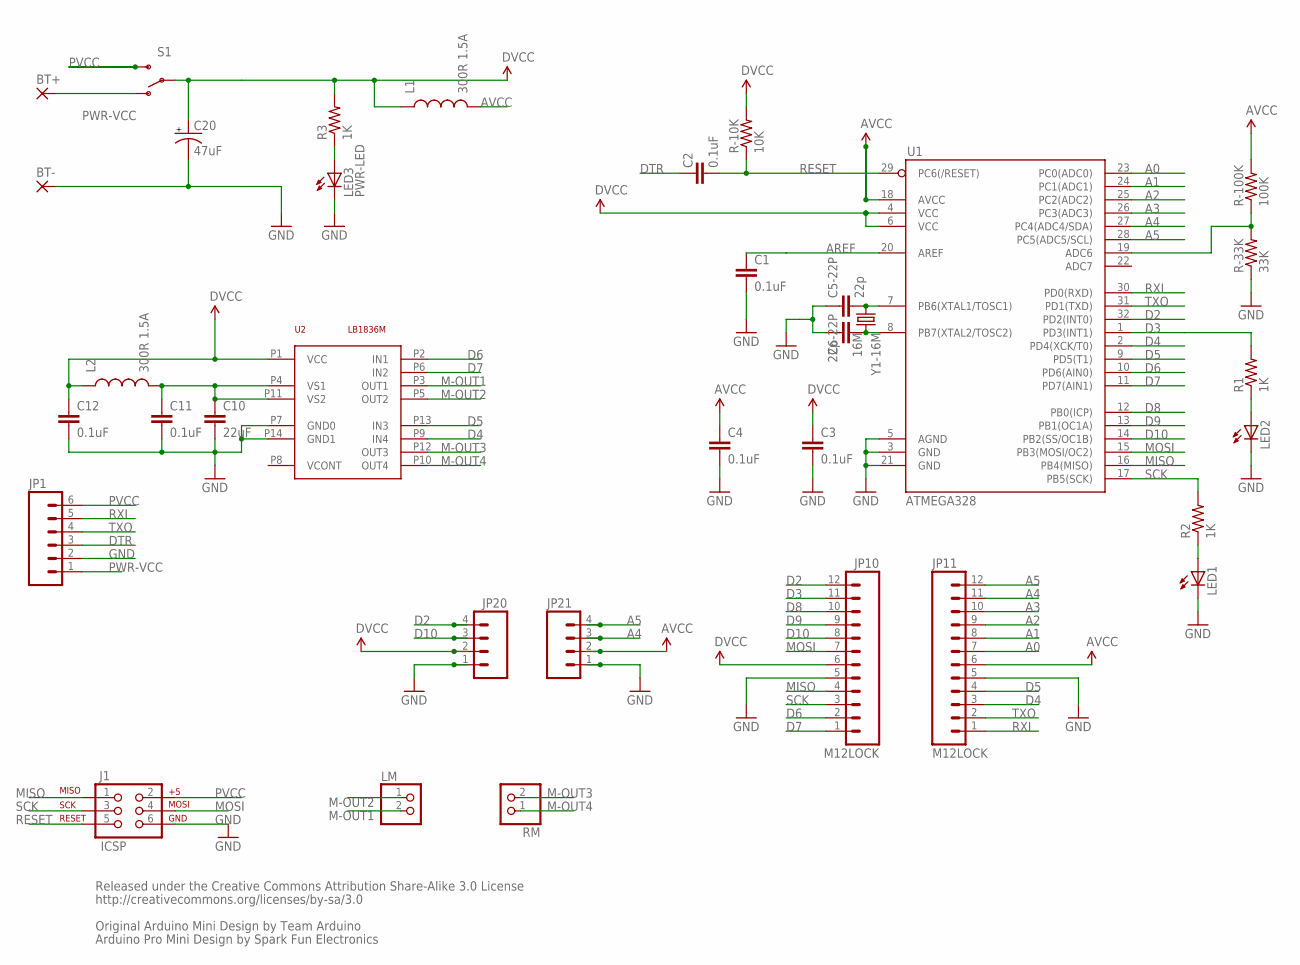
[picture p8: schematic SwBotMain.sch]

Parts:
BT+: SMD2; SMD1,27-2,54
BT-: SMD2; SMD1,27-2,54
C1, C2, C3, C4, C11, C12: 0.1uF; 0805
C5-22P, C6-22P: 22p; 0805
C10: 22uF; 1206
C20: 47uF; EIA3528
J1: ICSP; 2X3_LOCK
JP1: M06LOCK; 1X06_LOCK
JP10, JP11: M12LOCK; 1X12_LOCK
JP20, JP21: M04LOCK_LONGPADS; 1X04_LOCK_LONGPADS
L1, L2: 300R 1.5A; 0805
LED1, LED2: LEDCHIP-LED0805; CHIP-LED0805
LED3: PWR-LED; LED5MM
LM: PINHD-1X2; 1X02
R1, R2, R3: 1K; 0805
R-10K: 10K; 0805
R-33K: 33K; 0805
R-100K: 100K; 0805
RM: PINHD-1X2; 1X02
S1: SWITCH-SPDTPTH_LOCK; SWITCH-SPDT_LOCK.007S
U1: ATMEGA328; TQFP32-08
U2: LB1836M; MFP14S
Y1-16M: 16M; CRYSTAL-TXC-7A

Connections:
A0: JP11.7, U1.23 (PC0(ADC0))
A1: JP11.8, U1.24 (PC1(ADC1))
A2: JP11.9, U1.25 (PC2(ADC2))
A3: JP11.10, U1.26 (PC3(ADC3))
A4: JP11.11, JP21.3, U1.27 (PC4(ADC4/SDA))
A5: JP11.12, JP21.4, U1.28 (PC5(ADC5/SCL))
AREF: C1.1, U1.20 (AREF)
AVCC: C4.1, JP11.6, JP21.2, L1.2, R-100K.2, U1.18 (AVCC)
D2: JP10.12, JP20.4, U1.32 (PD2(INT0))
D3: JP10.11, R1.2, U1.1 (PD3(INT1))
D4: JP11.3, U1.2 (PD4(XCK/T0)), U2.P9 (IN4)
D5: JP11.4, U1.9 (PD5(T1)), U2.P13 (IN3)
D6: JP10.2, U1.10 (PD6(AIN0)), U2.P2 (IN1)
D7: JP10.1, U1.11 (PD7(AIN1)), U2.P6 (IN2)
D8: JP10.10, U1.12 (PB0(ICP))
D9: JP10.9, U1.13 (PB1(OC1A))
D10: JP10.8, JP20.3, U1.14 (PB2(SS/OC1B))
DTR: C2.2, JP1.3
DVCC: C3.1, C12.1, C20.A (+), JP10.6, JP20.2, L1.1, L2.1, R3.2, R-10K.2, S1.2, U1.4 (VCC), U1.6 (VCC), U2.P1 (VCC)
GND: BT-.1, C1.2, C3.2, C4.2, C5-22P.1, C6-22P.2, C10.2, C11.2, C12.2, C20.C (-), J1.6, JP1.2, JP10.5, JP11.5, JP20.1, JP21.1, LED1.C, LED2.C, LED3.K (C), R-33K.1, U1.3 (GND), U1.5 (AGND), U1.21 (GND), U2.P7 (GND0), U2.P14 (GND1)
M-OUT1: LM.2, U2.P3 (OUT1)
M-OUT2: LM.1, U2.P5 (OUT2)
M-OUT3: RM.2, U2.P12 (OUT3)
M-OUT4: RM.1, U2.P10 (OUT4)
MISO: J1.1, JP10.4, U1.16 (PB4(MISO))
MOSI: J1.4, JP10.7, U1.15 (PB3(MOSI/OC2))
unnamed: C6-22P.1, U1.8 (PB7(XTAL2/TOSC2)), Y1-16M.P$2 (2)
unnamed: C5-22P.2, U1.7 (PB6(XTAL1/TOSC1)), Y1-16M.P$1 (1)
unnamed: LED2.A, R1.1
unnamed: LED3.A, R3.1
unnamed: C10.1, C11.1, L2.2, U2.P4 (VS1), U2.P11 (VS2)
unnamed: R-33K.2, R-100K.1, U1.19 (ADC6)
unnamed: LED1.A, R2.1
PVCC: J1.2, JP1.6, S1.3 (S)
PWR-VCC: BT+.1, JP1.1, S1.1 (O)
RESET: C2.1, J1.5, R-10K.1, U1.29 (PC6(/RESET))
RXI: JP1.5, JP11.1, U1.30 (PD0(RXD))
SCK: J1.3, JP10.3, R2.2, U1.17 (PB5(SCK))
TXO: JP1.4, JP11.2, U1.31 (PD1(TXD))

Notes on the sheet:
Released under the Creative Commons Attribution Share-Alike 3.0 License
http://creativecommons.org/licenses/by-sa/3.0
Original Arduino Mini Design by Team Arduino
Arduino Pro Mini Design by Spark Fun Electronics

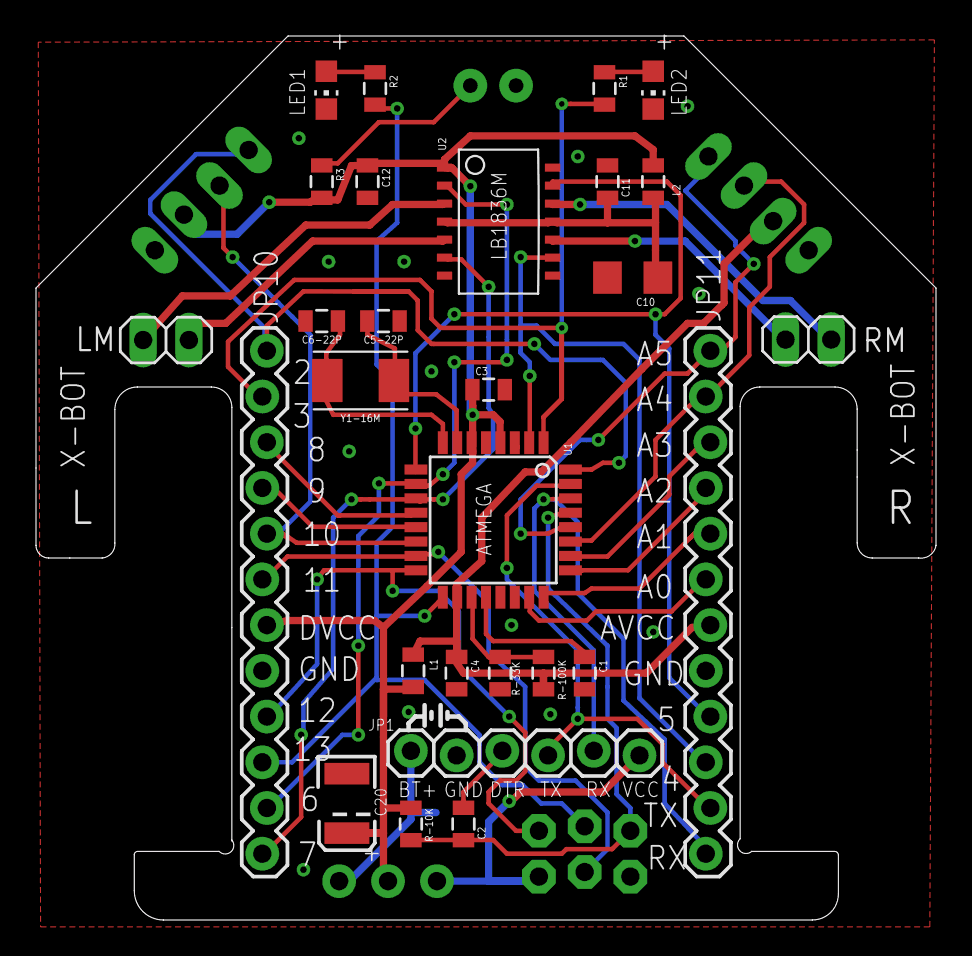
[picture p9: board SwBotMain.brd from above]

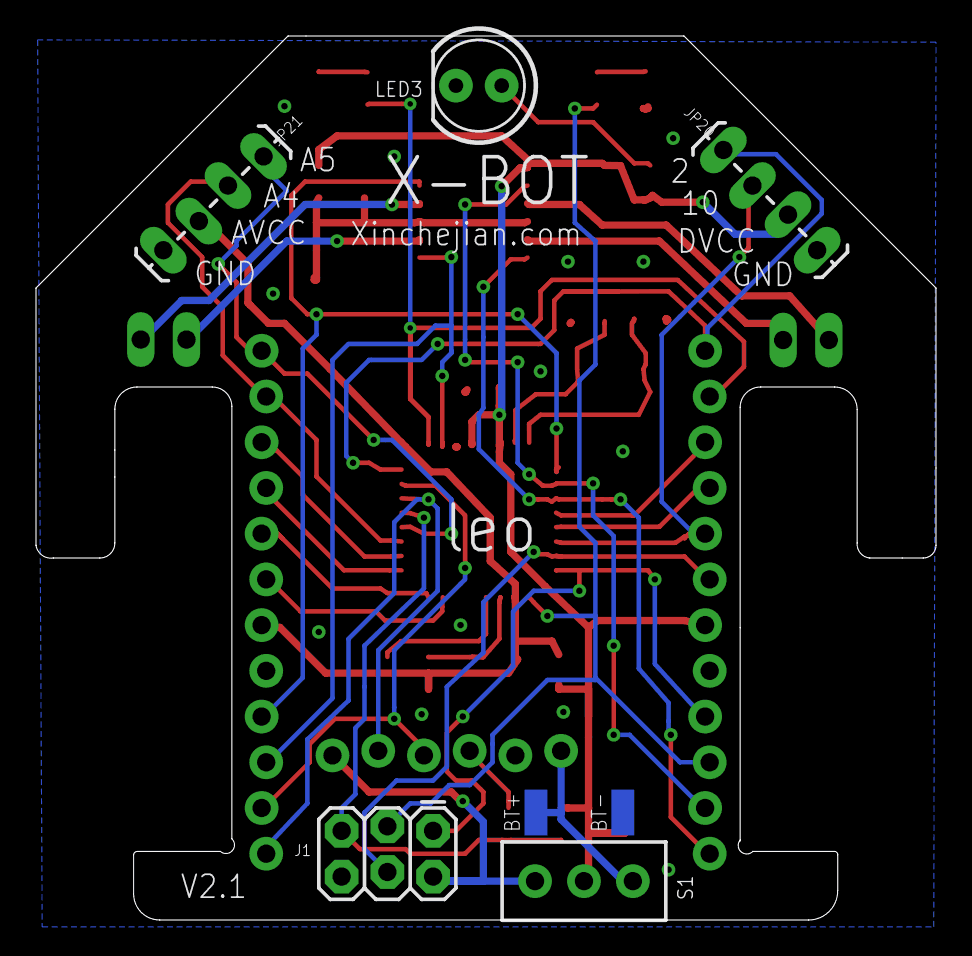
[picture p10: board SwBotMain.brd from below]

Board: 2 copper layers, 50.0 x 49.1 mm, 35 parts (7 on the bottom side), 39 nets.

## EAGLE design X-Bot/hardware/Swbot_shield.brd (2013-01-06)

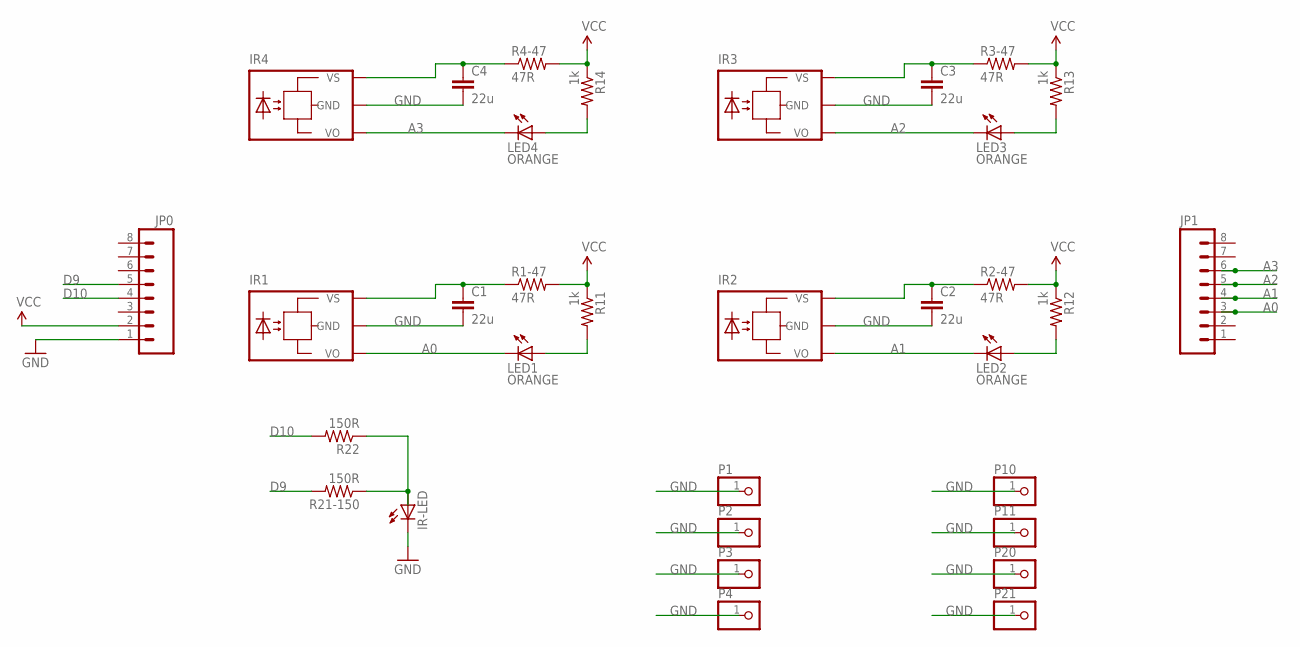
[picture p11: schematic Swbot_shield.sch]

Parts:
C1, C2, C3, C4: 22u; 1206
IR1, IR2, IR3, IR4: -NJL; TSOP
IR-LED: LED5MM
JP0, JP1: M08LOCK; 1X08_LOCK
LED1, LED2, LED3, LED4: ORANGE; CHIPLED_0805
P1, P2, P3, P4, P10, P11, P20, P21: PINHD-1X1; 1X01
R1-47, R2-47, R3-47, R4-47: 47R; 0805
R11, R12, R13, R14: 1k; 0805
R21-150, R22: 150R; 0805

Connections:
A0: IR1.VO, JP1.3, LED1.C
A1: IR2.VO, JP1.4, LED2.C
A2: IR3.VO, JP1.5, LED3.C
A3: IR4.VO, JP1.6, LED4.C
D9: JP0.5, R21-150.2
D10: JP0.4, R22.2
GND: C1.2, C2.2, C3.2, C4.2, IR1.GND, IR2.GND, IR3.GND, IR4.GND, IR-LED.K (C), JP0.1, P1.1, P2.1, P3.1, P4.1, P10.1, P11.1, P20.1, P21.1
unnamed: LED1.A, R11.2
unnamed: IR-LED.A, R21-150.1, R22.1
unnamed: LED2.A, R12.2
unnamed: LED3.A, R13.2
unnamed: C2.1, IR2.VCC (VS), R2-47.1
unnamed: LED4.A, R14.2
unnamed: C4.1, IR4.VCC (VS), R4-47.1
unnamed: C3.1, IR3.VCC (VS), R3-47.1
unnamed: C1.1, IR1.VCC (VS), R1-47.1
VCC: JP0.2, R1-47.2, R2-47.2, R3-47.2, R4-47.2, R11.1, R12.1, R13.1, R14.1

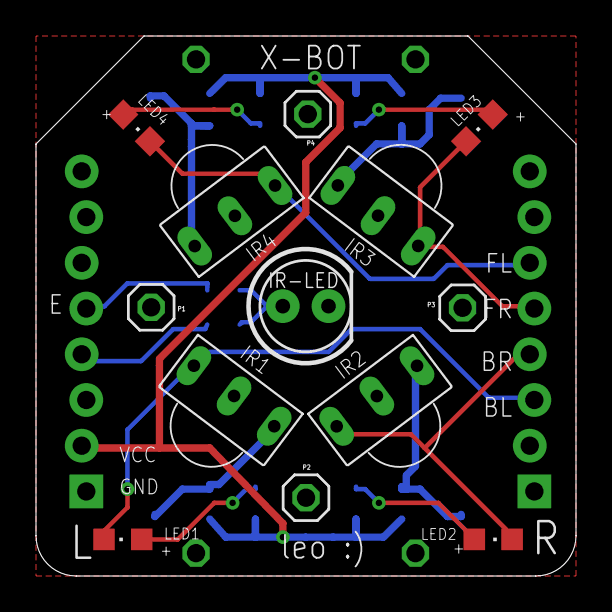
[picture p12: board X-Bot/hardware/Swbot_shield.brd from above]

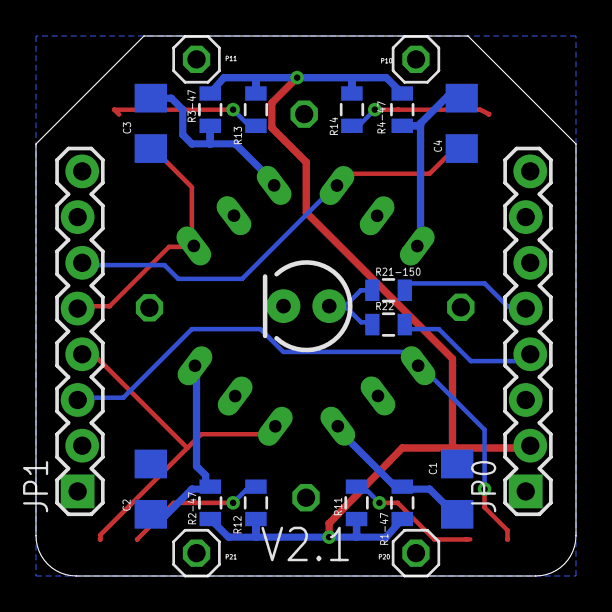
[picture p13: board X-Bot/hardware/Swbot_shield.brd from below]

Board: 2 copper layers, 30.0 x 30.0 mm, 33 parts (20 on the bottom side), 17 nets.

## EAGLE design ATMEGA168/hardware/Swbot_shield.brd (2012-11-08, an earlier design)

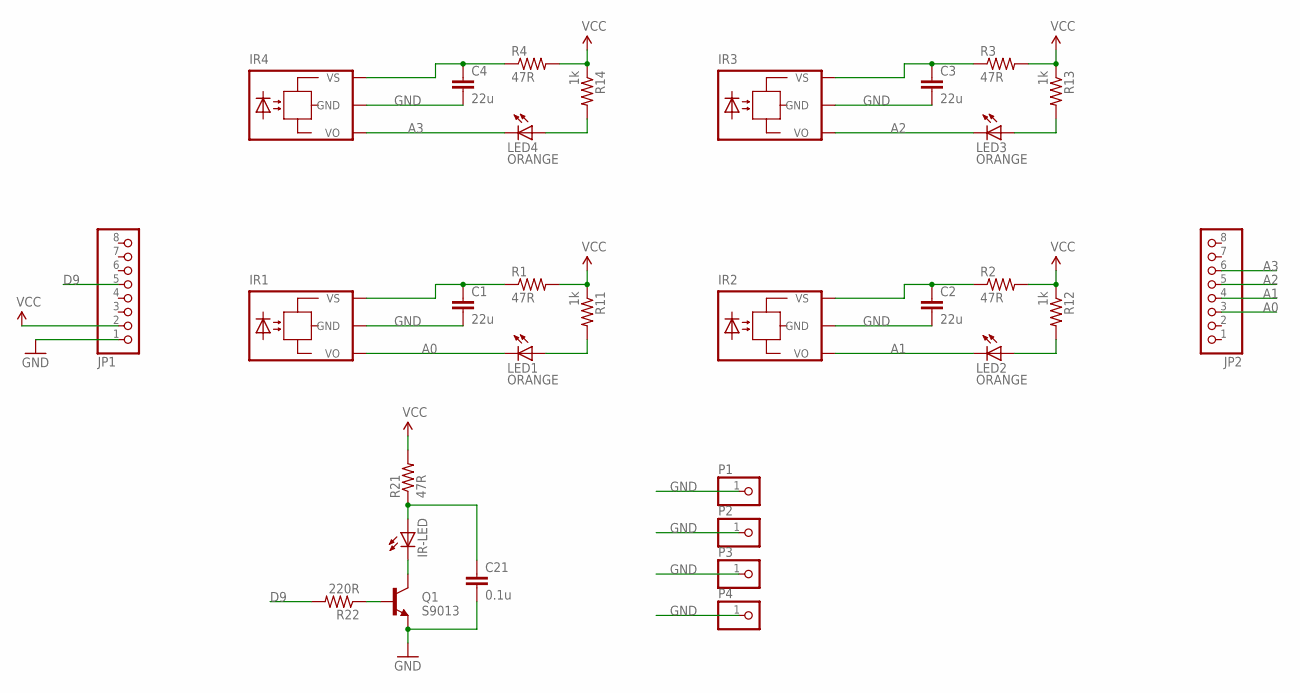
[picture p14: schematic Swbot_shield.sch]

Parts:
C1, C2, C3, C4: 22u; 1206
C21: 0.1u; 0805
IR1, IR2, IR3, IR4: -NJL; TSOP
IR-LED: LED5MM
JP1, JP2: PINHD-1X8; 1X08
LED1, LED2, LED3, LED4: ORANGE; CHIPLED_0805
P1, P2, P3, P4: PINHD-1X1; 1X01
Q1: S9013; SOT23-3
R1, R2, R3, R4, R21: 47R; 0805
R11, R12, R13, R14: 1k; 0805
R22: 220R; 0805

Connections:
A0: IR1.VO, JP2.3, LED1.C
A1: IR2.VO, JP2.4, LED2.C
A2: IR3.VO, JP2.5, LED3.C
A3: IR4.VO, JP2.6, LED4.C
D9: JP1.5, R22.2
GND: C1.2, C2.2, C3.2, C4.2, C21.2, IR1.GND, IR2.GND, IR3.GND, IR4.GND, JP1.1, P1.1, P2.1, P3.1, P4.1, Q1.2 (E)
unnamed: LED1.A, R11.2
unnamed: C21.1, IR-LED.A, R21.1
unnamed: IR-LED.K (C), Q1.3 (C)
unnamed: LED2.A, R12.2
unnamed: Q1.1 (B), R22.1
unnamed: LED3.A, R13.2
unnamed: C2.1, IR2.VCC (VS), R2.1
unnamed: LED4.A, R14.2
unnamed: C4.1, IR4.VCC (VS), R4.1
unnamed: C3.1, IR3.VCC (VS), R3.1
unnamed: C1.1, IR1.VCC (VS), R1.1
VCC: JP1.2, R1.2, R2.2, R3.2, R4.2, R11.1, R12.1, R13.1, R14.1, R21.2

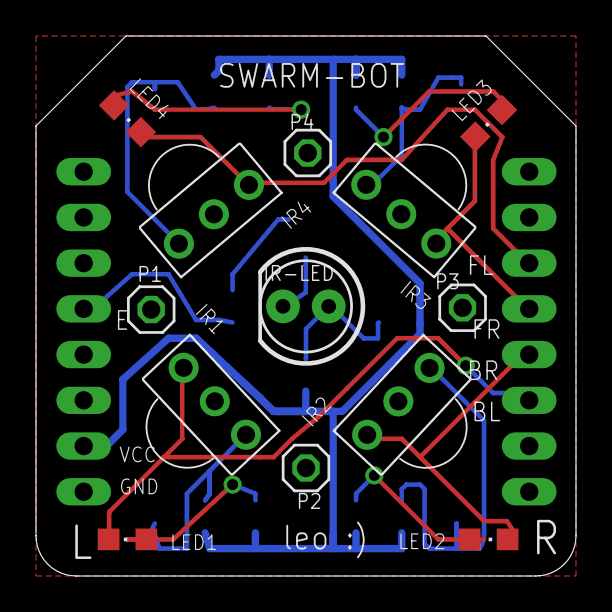
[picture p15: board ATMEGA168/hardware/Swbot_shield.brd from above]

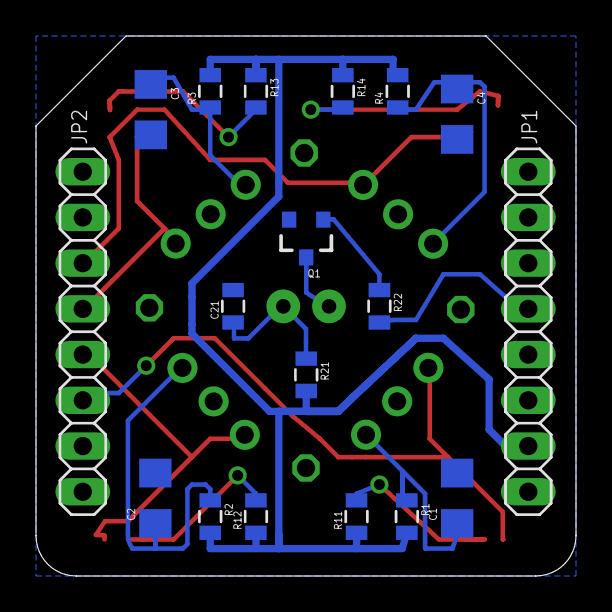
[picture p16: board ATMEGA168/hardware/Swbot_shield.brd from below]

Board: 2 copper layers, 30.0 x 30.0 mm, 31 parts (18 on the bottom side), 18 nets.

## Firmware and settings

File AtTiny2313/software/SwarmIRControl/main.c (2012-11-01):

//todo - also use these SAME #def's in the AtTiny receiver code!
// in the switch statement!!!!!
#define STOPCODE1 1        // button 1
#define STOPCODE2 0x36     // button stop

#define FWDCODE1  2        // button 2
#define FWDCODE2  0x35     // button play

#define REVCODE1  3        // button 3
#define REVCODE2  0x29     // button pause
#define REVCODE3  0x37     // button record

#define LFTCODE1  4        // button 4
#define LFTCODE2  0x32     // button fast forward

#define RGTCODE1  5        // button 5
#define RGTCODE2  0x34     // button fast rewind

#define SLTCODE1  0x3A     // button red
#define SRTCODE1  0x1C     // button blue

/*
            switch (Command)
            {

                case  STOPCODE1:
                case  STOPCODE2:
                {
                  break;
                }
                case  FWDCODE1:
                case  FWDCODE2:
                {
                  break;
                }
                case  REVCODE1:
                case  REVCODE2:
                case  REVCODE3:
                {
                  break;
                }
                case  LFTCODE1:
                case  LFTCODE2:
                {
                  break;
                }
                case  RGTCODE1:
                case  RGTCODE2:
                {
                  break;
                }
                case  SLTCODE1:
                case  SRTCODE1:
                {
                }
                default:
                {
                  break;
                }

*/




// todo - finish adding alternate Rx LED to read on - for physiacal layout - better reception - alternate wchich LED used

// after inactivy - spin a bit - in case can't receive IR at current position

// demo code timer/timeout not really workign!

//TODO - investigate if can decode MORE bits here - then can have more commands & groups (easy to add more in Arduino code)
//TODO - extend switch to handle all the cmd combinations



// *** This code MUST have AtTiny2313 running at **4MHz** so leave at factory default, or reset the fuse. ***
// code can probably be updated for 8MHz ......

#include "main.h"

/*
RC5 Address/ID/sys is 5 bits = 32, cmd is 6 bits = 64
    future:RC6 adds one more bit - but that also requires updated the IR decoding code.
Robot actions = #cmds (stop, f/b, 2xturn f/b, 2xspin f/b)=11 + allow for "more" actions - charge, follow me, .....

So start with:
    RC5
        - Address/ID/sys is 5 bits = 32 = 0x1F,     => SwarmRobot Group - each bit = 1 group - so a SwarmRobot can be in 0, 1 or many groups.
            0x0     not member of any group - ACT ON every COMMAND
            0x1     group 1 ACT on group 1 commands
            0x2     group 2
            0x4     group 3
            0x8     group 4
            0x10    group 5
            0x12    groups 5 & 2 ACT on group 2 & 5 commands
            ......

        - cmd is 6 bits = 64 = 0x3F                 => 0x0-0x1F = rc5Command
                                                    keep last bit spare for now - can use either for commands or for another group

    Note if need more than 32 SwarmRobots in a group, then just combine one or more groups - in the code.

above works well with custom Arduino transmitter

BUT - a commercial remote sends decimal numbers as command codes, not as per above!!!!
and more limited ability to set/choose group#


So implement group 0 + one #group, and specified cmd# in switch (cater for 2+ sets of arrow & play buttons <=> movement!!!!)



*/



//Ultimate aim is to put a groups for each robot in EEPROM, then use that to control group & individual behaviour
// This way code can be updated without overwriting group membership data!
// for now just KISS with a #define
#define MY_GROUP 2  // group 0 - execute ALL cmds!

#define MOTORS          // for debugging - comment out to turn off motors

// >>> Use of the serial works BUT
//      - speed is way off without crystal adn most terminals canto read
//      - using it INTERFERS WITH IO BIT BANGING SO THAT ir DECODING only works 1ST TIME, & MOTORS ONLY RUN FOR ~1/4 SECOND!
//#define SERIAL
#ifdef SERIAL
    #include "serial.h"
#endif

// These pins receive signals from the IR LEDs
#define IR_FC PD4              // IR LED Front Center
#define IR_R  PB0              // IR LED Rear
#define IR_FL PD6              // IR LED Front Left
#define IR_FR PB1              // IR LED Front Right



int irPIN[] = {6, 3};
#define IR_PIN PIND
int irPINIndex = 0;

//#define IR_IN  PD6             // Pin used for IR RC5 decode - using seperate (duplicate) definition to above - so can easily change!
//#define IR_PIN PIND            // port of pin above - used in IR decode function

/* All AtTiny2313 pins used for IR Rx

    *** take great care in the code!!!!- 1st two on portD, 2nd 2 on PortB

D6	8	PD4	P2 3	IR_FC
D8	11	PD6	P2 6	IR_FL

D9	12	PB0	P2 5	IR_R
D10	13	PB1	P2 4	IR_FR
*/



#define FLASHLED
#ifdef FLASHLED
    #define RX   PD0
    #define TX   PD1
#endif


// temp debug - do not use this AND FLASHLED!!!!!!
//#define CMD_FLASHLED
#ifdef CMD_FLASHLED
    #define RX   PD0
    #define TX   PD1
#endif




//Motor pin definitions
#define M_LF PA1             // Motor Left Front
#define M_LB PA0             // Motor Left Back
#define M_RF PD2             // Motor Right Front
#define M_RB PD3             // Motor Right Back

#define M_REn PD5            // Motor Right Enable
#define M_LEn PB2            // Motor Left Enable

#define ROBOT_CMD_MASK  0x3F
#define ROBOT_SYS_MASK  0x1F


volatile uint8_t inttemp;
volatile uint8_t timerL;
volatile uint8_t timerH;

uint16_t detect(void);
void main_init(void);
void actionLogic(int command);


#ifdef MOTORS
void stopNow(void);
void forward(void);
void backward(void);
void turnLeft(void);
void turnRight(void);
void spinLeft(void);
void spinRight(void);
#endif

//********************************************************************************
//********************************************************************************
int demoCode = 0;       // use to trigger demo mode.
#define DEMO 180        // just some magic number that means run demo mode
#define DEMO_DELAY_COUNT 2      // how long each action runs for
#define DEMO_ACTION_COUNT 13
int demoAction[] = {0x3A, 0x3A, 1, 0x1C, 0x1C, 1, 0x3A, 1, 0x1C, 1, 4, 1, 5, 1};
int demoActionIndex = 0;
int demoDelayCount = 0;
//********************************************************************************
//********************************************************************************

int main(void)
{
#ifdef SERIAL
  char sys[3];
  char cmd[3];
#endif
  uint16_t rc5Frame;
  uint8_t rc5Toggle;
  uint8_t rc5Id;
  uint8_t rc5Command;

    // these two depend upon the time in detect() attempting to read start of an IR code.
    // this is a variable time that is PROBABLY between 3.5 & 131mS
  int timoutCounter = 0;
  int timeout = 100;            // how many counts to get before timeout is triggered.

  main_init();
    #ifdef SERIAL
  serial_init(9600);
    #endif
  sei();
    #ifdef SERIAL
  serial_puts("RC5 IR Decoder\r\n");
    #endif
  while(1) {
    rc5Frame = detect();
    if (rc5Frame != 0xFFFF) {
        timoutCounter = 0;                  // reset timeOut counter - because command has been received.
        rc5Id = (rc5Frame >> 6) & ROBOT_SYS_MASK;
        rc5Command = rc5Frame & ROBOT_CMD_MASK;
        rc5Toggle = (rc5Frame >> 11) & 0x01;

        // if received ID matches any group this robot belongs to, do the action specified!
        if ((rc5Id == MY_GROUP) || (rc5Id == 0)) {
            actionLogic(rc5Command);
        }

    #ifdef FLASHLED
    //  bit/LED off &=0, on |=1
    PORTD |= (1 <<RX);          // turn LED ON
    #endif

    #ifdef SERIAL
      utoa(rc5Id, sys, 10);
      utoa(rc5Command, cmd, 10);

      serial_puts("sys: ");
      serial_puts(sys);
      serial_puts(" cmd: ");
      serial_puts(cmd);
      serial_puts(" rc5Toggle: ");
      serial_putc(rc5Toggle + '0');
      serial_puts("\r\n");
    #endif
    }
    else {
        //count how many times "tried" to decode & failed
        if (timoutCounter++ > timeout) {
            #ifdef MOTORS
            stopNow();
            #endif
            demoCode = 0;
            timoutCounter = 0;
        }
        #ifdef FLASHLED
        PORTD &= ~(1 <<RX);          // turn LED off
        #endif

        #ifdef CMD_FLASHLED
        PORTD &= ~(1 <<RX);          // turn LED off
        #endif

        if (demoCode > DEMO){
            // so run the demo action at current index
            if (demoAction[demoActionIndex] == 1)
                stopNow();  // because using actionLogic(1)  - exits demo mode!
            else
                actionLogic(demoAction[demoActionIndex]);
            //now update counter/index as required
            if (++demoDelayCount > DEMO_DELAY_COUNT) {
                //when delay times out - reset delay counter & increment for next action
                demoDelayCount =0;
                if (++demoActionIndex > DEMO_ACTION_COUNT) demoActionIndex = 0;
            }
        }
    }
  }

  //stopNow();
  return 0;
}


void actionLogic(int command){
            switch (command)
            {

                case 1:
                case 0x36:
                {
#ifdef MOTORS
                    stopNow();
#endif
                    demoCode =0;    // exit demo mode!
                    demoDelayCount = 0;
                    demoActionIndex = 0;
                    break;
                }
                case 2:
                case 0x35:
                {
#ifdef MOTORS
                    forward();
#endif
                    break;
                }
                case 3:
                case 0x29:
                case 0x37:
                {
#ifdef MOTORS
                    backward();
#endif
                    break;
                }
                case 4:
                case 0x32:
                {
#ifdef MOTORS
                    turnLeft();
#endif
                    break;
                }
                case 5:
                case 0x34:
                {
#ifdef MOTORS
                    turnRight();
#endif
                    break;
                }
                case 0x3A:
                {
#ifdef MOTORS
                    spinLeft();
#endif
                    break;
                }
                case 0x1C:
                {
#ifdef MOTORS
                    spinRight();
#endif
                    break;
                }


// here is code to trigger demo mode.
                case 9:
                {
                     demoCode +=9;
                   break;
                }
                default:
                {
#ifdef MOTORS
                    //stopNow();
#endif
                    break;
                }
            }
}


void main_init(void)
{
  // clocked at CK @ 4MHZ
  TCCR0B = _BV(CS00);
  // enable over flow interrupt
  TIMSK = _BV(TOIE0);

    #ifdef MOTORS
    // initialise all the motor control pins
    DDRA |= (1 <<M_LF);         //Set as output
    DDRA |= (1 <<M_LB);         //Set as output
    DDRD |= (1 <<M_RF);         //Set as output
    DDRD |= (1 <<M_RB);         //Set as output

    DDRD |= (1 <<M_REn);        //Set as output
    DDRB |= (1 <<M_LEn);        //Set as output

    stopNow();                  //// all motor controller bits = 0 - ie off/disabled
    #endif

    #ifdef FLASHLED
    DDRD |= (1 <<RX);         //Set as output
    PORTD &= ~(1 <<RX);        // LED OFF
    #endif

    #ifdef CMD_FLASHLED
    DDRD |= (1 <<RX);         //Set as output
    PORTD &= ~(1 <<RX);        // LED OFF
    #endif
}



// Below here are all the motor control functions
#ifdef MOTORS
void stopNow(){
  PORTA &= ~(1 <<M_LB);
  PORTA &= ~(1 <<M_LF);
  PORTD &= ~(1 <<M_RB);
  PORTD &= ~(1 <<M_RF);

  PORTD &= ~(1 <<M_REn);
  PORTB &= ~(1 <<M_LEn);
}

void forward(){
  PORTA &= ~(1 <<M_LB);
  PORTA |= (1 <<M_LF);
  PORTD &= ~(1 <<M_RB);
  PORTD |= (1 <<M_RF);

  PORTD |= (1 <<M_REn);
  PORTB |= (1 <<M_LEn);
}

void backward(void){
  PORTA |= (1 <<M_LB);
  PORTA &= ~(1 <<M_LF);
  PORTD |= (1 <<M_RB);
  PORTD &= ~(1 <<M_RF);

  PORTD |= (1 <<M_REn);
  PORTB |= (1 <<M_LEn);
}

void turnLeft(void){
  PORTA &= ~(1 <<M_LB);
  PORTA |= (1 <<M_LF);
  PORTD &= ~(1 <<M_RB);
  PORTD &= ~(1 <<M_RF);

  PORTD |= (1 <<M_REn);
  PORTB |= (1 <<M_LEn);
}

void turnRight(void){
  PORTA &= ~(1 <<M_LB);
  PORTA &= ~(1 <<M_LF);
  PORTD &= ~(1 <<M_RB);
  PORTD |= (1 <<M_RF);

  PORTD |= (1 <<M_REn);
  PORTB |= (1 <<M_LEn);
}

void spinLeft(void){
  PORTA &= ~(1 <<M_LB);
  PORTA |= (1 <<M_LF);
  PORTD |= (1 <<M_RB);
  PORTD &= ~(1 <<M_RF);

  PORTD |= (1 <<M_REn);
  PORTB |= (1 <<M_LEn);
}

void spinRight(void){
  PORTA |= (1 <<M_LB);
  PORTA &= ~(1 <<M_LF);
  PORTD &= ~(1 <<M_RB);
  PORTD |= (1 <<M_RF);

  PORTD |= (1 <<M_REn);
  PORTB |= (1 <<M_LEn);
}


#endif



// Below here = IR decode
ISR(TIMER0_OVF_vect)
{
  timerL++;
  inttemp++;
  if (inttemp == 0) {
    timerH++;
  }
}

uint16_t detect(void)
{
  uint16_t rc5Frame;
  uint8_t i, temp, ref1, ref2;
  inttemp = 0;
  timerH = 0;

  detect1:
    timerL = 0;

    while(timerL < 55) { // idle high for 3.52ms
      if (timerH > 8) { // no success in 131.072ms, time to give up
        goto fault;
      }

      if (bit_is_clear(IR_PIN, irPIN[irPINIndex])) {
        goto detect1;
      }
    }

    while(bit_is_set(IR_PIN, irPIN[irPINIndex])) { // start1:
      if (timerH >= 8) { // no success in 131.072ms, time to give up
        goto fault;
      }
    }

    timerL = 0;
    while(bit_is_clear(IR_PIN, irPIN[irPINIndex])) { // start2:
      if (timerL >= 17) { // high for excess of 1088us
        goto fault;
      }
    }

    temp = timerL;
    timerL = 0;

    ref1 = temp;  // half bit time
    ref1 >>= 1;   // quarter bit time
    ref2 = ref1;
    ref1 += temp; // 3/4 bit time
    temp <<= 2;   // 1 bit time
    ref2 += temp; // 5/4 bit time

    while(bit_is_set(IR_PIN, irPIN[irPINIndex])) { // start3:
      if (timerL >= ref1) {
        goto fault;
      }
    }

    //timerL = 0;
    rc5Frame = 0;

    // sample the 12 data bits
    for(i=0;i<12;i++)
    {
      timerL = 0;

      while (timerL < ref1)
        ;

      rc5Frame <<= 1;
      if (bit_is_set(IR_PIN, irPIN[irPINIndex])) {
        // store a 1
        rc5Frame |= 0x01;

        while(bit_is_set(IR_PIN, irPIN[irPINIndex])) {
          if (timerL > ref2) {
            goto fault;
          }
        }
      } else {
        // no action required to store a 0
        while(bit_is_clear(IR_PIN, irPIN[irPINIndex])) {
           if (timerL > ref2) {
             goto fault;
           }
         }
      }
    }
    // rc5Frame == 12 bits stored.
    return rc5Frame;
  fault:
    // return fault code
    return 0xFFFF;
}

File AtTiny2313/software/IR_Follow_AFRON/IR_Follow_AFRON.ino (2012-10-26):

/*
  Xinchejian Hackerspace Shanghai SwarmRobot http://wiki.xinchejian.com/wiki/Swarm_robots/

  Implements core motor driver functionality and simple InfraRed (IR) chasing.

  Licence CC by SA

  Sofware version              IR1.01  Date:- 2012-08-30

  Uses Hardware:-
    - Motor driver PCB version     Date:- 2012-08
    - IR shield version            Date:- 2012-08
*/

/*
  Release notes for this version:

  - Added Notes_Tips_ToDO files so the main code looks simpler and is not overwhelming!
  - Lots of comments added and things shuffled about to make things more readable
  - Added #define SPIN to allow SwarmBot to turn on the spot (one wheel goes forward, other backwards),
    else pivot on one wheel while other drives forwards
  - Discarded changes in previous version as motor drive logic was not working

*/


// *** This code MUST have AtTiny2313 running at 8MHz so change from factory default of 4MHz!! ***
// this can be done in Arduino programmign GUI by Tools menu - BurnBootloader.



//********************************************************************************************************
//Global IO Pin and variable definitions

// These pins flash to show serial data is being received (Rx) or transmitted (Tx)
// Also can be used to show IR signals received from left, right, front (both LED). No indication for reverse.
#define RxPin 0
#define TxPin 1
#define R_LED RxPin          // using less confusing name for IR signal flashing
#define L_LED TxPin          // using less confusing name for IR signal flashing

// These pins receive signals from the IR LEDs
#define IR_FC 6              // IR LED Front Center
#define IR_FL 8              // IR LED Front Left
#define IR_R 9               // IR LED Rear
#define IR_FR 10             // IR LED Front Right

//These pins are connected to the L293D motor controller
#define M_LF 2               // Motor Left Front
#define M_LB 3               // Motor Left Back
#define M_RF 4               // Motor Right Front
#define M_RB 5               // Motor Right Back
#define M_REn 7              // Motor Right ENABLE
#define M_LEn 11             // Motor Left ENABLE

#define PWM                  // use PWM motor speed control, else just full power!
#define SPD_FAST 255         // setting for PWM motor control Fast
#define SPD_NORMAL 200       // setting for PWM motor control Normal
#define SPD_SLOW 100         // setting for PWM motor control Slow

#define SPIN true            // Turn on the spot (one wheel goes forward, other backwards),
                             // else pivot on one wheel while other drives forwards

#define FLASH_ON_IR          // if this is defined, then flash the Rx &/or Tx LEDs to indicate direction of received IR.
                             // This way you can skip the four LEDs on the IR shield!
                             // no flashing for rear signal!
//********************************************************************************************************


void setup() {

// Set the Attiny IO pin modes, Note PWM pins do not require initialisation.
  pinMode(M_LF, OUTPUT);
  pinMode(M_LB, OUTPUT);
  pinMode(M_RF, OUTPUT);
  pinMode(M_RB, OUTPUT);

  #ifndef PWM
  // just testing no PWM, L293 always enabled!
  pinMode(M_REn, OUTPUT);
  pinMode(M_LEn, OUTPUT);
  digitalWrite(M_REn, HIGH);    // Low is disabled
  digitalWrite(M_LEn, HIGH);    // Low is disabled
  #endif

  pinMode(IR_FC, INPUT);        // Front Center IR LED input Attiny pin
  pinMode(IR_FL, INPUT);        // Front Left IR LED input Attiny pin
  pinMode(IR_FR, INPUT);        // Front Right IR LED input Attiny pin
  pinMode(IR_R,  INPUT);        // Rear IR LED input Attiny pin

  pinMode(RxPin, OUTPUT);
  pinMode(TxPin, OUTPUT);

  stopNow();                    //make sure all pins initialised & both motors stopped

  //Moving forward for short time to show this SwarmBot is working OK!
  forward(SPD_FAST);
  delay(300);
}


void loop() {

  // Read all the IR LED outputs
  boolean IR_front = digitalRead(IR_FC);
  boolean IR_left = digitalRead(IR_FL);
  boolean IR_right = digitalRead(IR_FR);
  boolean IR_rear = digitalRead(IR_R);

  // Move the SwarmBot in direction of the 'best' IR signal
  if( (IR_front == LOW) && ( 0 == (IR_left ^ IR_right)) ) {
    forward(SPD_FAST);
    delay(100);
  }else if(IR_left == LOW) {
    turnLeft(SPD_FAST, SPIN);
    delay(100);
  }else if(IR_right == LOW) {
    turnRight(SPD_FAST, SPIN);
    delay(100);
  }else if(IR_rear == LOW) {
    backward(SPD_FAST);
    delay(100);
  }else {
    stopNow();
  }

  #ifdef FLASH_ON_IR
  //Turn both LEDs OFF - so they flash a bit - just for showing off!
  digitalWrite(R_LED, LOW);
  digitalWrite(L_LED, LOW);
  #endif
}
// **************** END of main loop program ****************



// *** Below here are all the motor control functions ***
void stopNow(){
  digitalWrite(M_LB, 0);
  digitalWrite(M_LF, 0);
  digitalWrite(M_RB, 0);
  digitalWrite(M_RF, 0);

  #ifdef PWM
  analogWrite(M_REn, 0);            // PWM pin
  analogWrite(M_LEn, 0);            // PWM pin
  #endif
}



void forward(int speed){
  digitalWrite(M_LB, 0);
  digitalWrite(M_LF, HIGH);
  digitalWrite(M_RB, 0);
  digitalWrite(M_RF, HIGH);

  #ifdef PWM
  analogWrite(M_REn, speed);            // PWM pin
  analogWrite(M_LEn, speed);            // PWM pin
  #endif

  #ifdef FLASH_ON_IR
  //turn both LEDs on
  digitalWrite(R_LED, HIGH);
  digitalWrite(L_LED, HIGH);
  #endif
}



void backward(int speed){
  digitalWrite(M_LF, 0);
  digitalWrite(M_LB, HIGH);
  digitalWrite(M_RF, 0);
  digitalWrite(M_RB, HIGH);

  #ifdef PWM
  analogWrite(M_REn, speed);            // PWM pin
  analogWrite(M_LEn, speed);            // PWM pin
  #endif

  //NO LEDs on!!
}



void turnLeft(int speed, bool spin){
  if (spin){
    // left wheel in reverse
    digitalWrite(M_LF, 0);
    digitalWrite(M_LB, HIGH);
  }
  // Right wheel forwards
  digitalWrite(M_RB, 0);
  digitalWrite(M_RF, HIGH);

  #ifdef PWM
  analogWrite(M_REn, speed);            // PWM pin
  analogWrite(M_LEn, speed);            // PWM pin
  #endif

  #ifdef FLASH_ON_IR
  digitalWrite(L_LED, HIGH);            //turn Left LED on
  #endif
}



void turnRight(int speed, bool spin){
  // Left wheel forwards
  digitalWrite(M_LB, 0);
  digitalWrite(M_LF, HIGH);
  if (spin){
    // Right wheel in reverse
    digitalWrite(M_RF, 0);
    digitalWrite(M_RB, HIGH);
  }
  #ifdef PWM
  analogWrite(M_REn, speed);          // PWM pin
  analogWrite(M_LEn, speed);          // PWM pin
  #endif

  #ifdef FLASH_ON_IR
  digitalWrite(R_LED, HIGH);        //turn right LED on
  #endif
}

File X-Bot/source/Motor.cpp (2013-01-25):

/*
                          IR-Swarmbot Software

    Copyright (C) <2012>  <Leo Yan>

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
    Contact: leo.yan.cn@gmail.com
*/

#include "Arduino.h"
#include "SwarmRobot.h"
#include "Motor.h"

/* Analysis of critical resource:
1.
critical resource:  SpeedVal - (type is uint8_t)

main thread:   SetSpeed()
timer thread:  TimerProc()->if RunCnt==0 ->Stop()

2.
critical resource:  RunCnt - (type is uint16_t)

main thread:   SetMoveDistance()
               SetRotateAngle()

timer thread:  TimerProc()-> if SpeedVal!= 0 ->Stop()

$ conclude:
1. when setting, RunCnt must be set before SpeedVal
2. when clearing, no constraint

 */



/*public*/
BiMotor::BiMotor( )

{
    MotorPin[MOTOR_INDEX_L].DriverA = MOTOR_L_DIRPINA;
    MotorPin[MOTOR_INDEX_L].DriverB = MOTOR_L_DIRPINB;
    MotorPin[MOTOR_INDEX_R].DriverA = MOTOR_R_DIRPINA;
    MotorPin[MOTOR_INDEX_R].DriverB = MOTOR_R_DIRPINB;

    Stop();
    //pin initialization

    pinMode(MotorPin[MOTOR_INDEX_L].DriverA,OUTPUT);
    pinMode(MotorPin[MOTOR_INDEX_L].DriverB,OUTPUT);
    pinMode(MotorPin[MOTOR_INDEX_R].DriverA,OUTPUT);
    pinMode(MotorPin[MOTOR_INDEX_R].DriverB,OUTPUT);

    LastMoveDirection = MT_FORWARD;
    LastMovePara = 0;

    StepRepeatState = false;
    RotateRepeatState = false;
    RotatePingPangState = false;

}


/* MT_STOP is also consider as moving in order to balance time. */
bool BiMotor::isMoving()
{
    return ( (MT_SPEED_ZERO == SpeedVal)? false : true  );
}

bool BiMotor::isStepRepeat()
{
    return StepRepeatState;
}

bool BiMotor::isRotateRepeat()
{
    return RotateRepeatState;
}

bool BiMotor::isRotatePingPang()
{
    return RotatePingPangState;
}


void BiMotor::GetMoveAciton( MTMovDir_enum &Direction, uint8_t &Para )
{
    Direction = LastMoveDirection;
    Para = LastMovePara;
}



void BiMotor::Move( MTMovDir_enum Direction, uint8_t Para, MTSpeed_enum Speed )
{

    if ( 0 == Para )
    {
        ASSERT_T(0);
        return;
    }

    switch ( Direction )
    {
    case MT_FORWARD:
    case MT_BACKWARD:
    case MT_STOP:
        Walk( Direction, Para );
        break;

    case MT_CLOCKWISE:
    case MT_ANTICLOCK:
        Rotate( Direction, Para );
        break;
        
    case MT_TURNLEFT:
    case MT_TURNRIGHT:
        //todo
        break;

    default:
        ASSERT_T(0);
    }

    /** RunCnt must be set before SpeedVal**/
    SetSpeed(Speed);

    Run();

    Statistic( Direction, Para);

}

void BiMotor::Statistic( MTMovDir_enum Direction, uint8_t Para )
{
    static uint8_t RepeatCnt = 0;
    static uint8_t RotatePingPangCnt = 0;

    /**judge repeated single action**/
    if ( LastMoveDirection != Direction )
    {
        RepeatCnt = 0;
        StepRepeatState = false;
        RotateRepeatState = false;
    }
    else
    {
        if ( RepeatCnt < 255 )
        {
            RepeatCnt++;
        }
    }

    if ( MT_FORWARD == Direction )
    {
        StepRepeatState = (RepeatCnt >= REPEATED_STEP_THRESHOLD) ? true : false;
    }
    else if ( (MT_CLOCKWISE == Direction) || (MT_CLOCKWISE == Direction) )
    {
        RotateRepeatState = (RepeatCnt >= REPEATED_ROTATE_THRESHOLD) ? true : false;
    }
    else
    {
        //nothing
    }

    /**judge rotate PingPong state**/

    if ( (MT_CLOCKWISE != Direction) && (MT_ANTICLOCK != Direction) )
    {
        RotatePingPangCnt = 0;
    }
    else
    {
        if ( (LastMoveDirection != Direction)
                && (RotatePingPangCnt < 255) )
        {   //the fist is maybe incorrect, but it isn't a matter if PINGPANG_ROTATE_THRESHOLD > 2.

            RotatePingPangCnt++;
        }
    }

    RotatePingPangState = (RotatePingPangCnt >= PINGPANG_ROTATE_THRESHOLD) ? true : false;

    /**store info**/
    LastMoveDirection = Direction;
    LastMovePara = Para;
}


/* Walk == Go straight */

inline void BiMotor::Walk(
        MTMovDir_enum Direction,
        uint8_t Distance         //the unit is 1 cm
        )
{
    MTSingleAct_enum Action;
    uint8_t i;


    /*set direction*/
    switch(Direction)
    {
    case MT_FORWARD:
        Action = MT_ACTION_FORWORD;
        break;

    case MT_BACKWARD:
        Action = MT_ACTION_BACKWORD;
        break;

    case MT_STOP:
        Action = MT_ACTION_STOP;
        break;

    default:
        return;

    }

    for (i = 0; i < MOTOR_NUM; ++i )
    {
        SetSingleMotorAction( i, Action);
    }

    RunCnt = (uint32_t)Distance * MT_STEP_ONE;      // todo: to add measure program later
}


/*
 *
 */

inline void BiMotor::Rotate(
        MTMovDir_enum Direction,
        uint8_t Angle              // the unit is 10 degree
        )
{

    /*set dirction*/
    switch(Direction)
    {
    case MT_CLOCKWISE:
        SetSingleMotorAction( MOTOR_INDEX_L, MT_ACTION_FORWORD);
        SetSingleMotorAction( MOTOR_INDEX_R, MT_ACTION_BACKWORD);
        break;

    case MT_ANTICLOCK:
        SetSingleMotorAction( MOTOR_INDEX_L, MT_ACTION_BACKWORD);
        SetSingleMotorAction( MOTOR_INDEX_R, MT_ACTION_FORWORD);
        break;

    default:
        ; //error

    }

    RunCnt = (uint32_t)Angle * MT_ROTATE_ONE;  // todo: to add measure program later
}

inline void BiMotor::Stop( )
{
    uint8_t i;

    RunCnt = 0;
    SpeedVal = MT_SPEED_ZERO;

    for (i = 0; i < MOTOR_NUM; ++i )
    {
        SetSingleMotorAction( i, MT_ACTION_STOP );
    }
}

/*private*/
inline void BiMotor::Run( )
{
    /*if the driver chip has Enable pin, add code here*/
}

/*
 * to control the rotation of single motor
 */

void BiMotor::SetSingleMotorAction( uint8_t Index, MTSingleAct_enum Action )
{

    uint8_t DriverA, DriverB;
    //assert para

    DriverA = MotorPin[Index].DriverA;
    DriverB = MotorPin[Index].DriverB;

    switch (Action)
    {
    case MT_ACTION_FORWORD:
        digitalWrite(DriverA, HIGH);
        digitalWrite(DriverB, LOW);
        break;
    case MT_ACTION_BACKWORD:
        digitalWrite(DriverA, LOW);
        digitalWrite(DriverB, HIGH);
        break;
    case MT_ACTION_STOP:
        digitalWrite(DriverA, LOW);
        digitalWrite(DriverB, LOW);
        break;
    default:
        ; //error
    }

}


inline void BiMotor::SetSpeed( MTSpeed_enum Speed )
{
    SpeedVal = Speed;
}


/*
 * to control the distance by time
 */
void BiMotor::TimerProc()
{
    if ( MT_SPEED_ZERO == SpeedVal )
    {
        return;
    }

    if( 0 == RunCnt )
    {
        Stop();
    }
    else
    {
        RunCnt --;
    }

}

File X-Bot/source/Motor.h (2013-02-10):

/*****
 * Direction based on the steering direction. you is the driver.
 *
 *
 *****/

#ifndef Motor_h
#define Motor_h

#include <inttypes.h>

#if _DEBUG
#define _DEBUG_MT 0
#endif


#define MOTOR_L_DIRPINA 7  //The control direction pin of left motor (connecting to LM 1A pin)
#define MOTOR_L_DIRPINB 6
#define MOTOR_R_DIRPINA 4
#define MOTOR_R_DIRPINB 5


//#define MT_DUTY(Val) _SFR_MEM16(OCR1A_MEM) = (uint16_t)((uint32_t)(Val)*ICR1)/255
#define MT_DUTY(Val) OCR1A = (uint16_t)( ((uint32_t)(Val)*ICR1)>>8 )




/* Near Distance = the distance of near detecting = as 1.5 times as lenth of robot, on the condition of suggest material
 */

#define MT_STEP_ONE 600   // 400 for 0.5cm

#define MT_ROTATE_ONE 400  // 10degre  180degree = 18*350

#define MT_ANGEL_UNIT 10    //10degre

#define MT_DEGREE(a) ((a)/MT_ANGEL_UNIT)

#define REPEATED_STEP_THRESHOLD 8
#define REPEATED_ROTATE_THRESHOLD 37
#define PINGPANG_ROTATE_THRESHOLD 3  // It must be lager than 2

#if (PINGPANG_ROTATE_THRESHOLD < 3)
#error
#endif

typedef enum
{
    MT_STOP,
    MT_FORWARD,
    MT_BACKWARD,
    MT_CLOCKWISE,
    MT_ANTICLOCK,
    MT_TURNLEFT,   //One wheel is fixed, one is forward.
    MT_TURNRIGHT
}MTMovDir_enum;


/*to control the duty of PWM. the value must be less than 255
 * it is unusable for no enable function chip, eg:LM1836
 * */
typedef enum MT_SPEED
{
    MT_SPEED_ZERO = 0,
    MT_SPEED_SLOW = 230,    //  duty = MT_SLOW/255
    MT_SPEED_NORMAL = 250,
    M_SPEED_FAST = 255    
}MTSpeed_enum;

#define ANGLE_RANDOM 0  //0-180 degree


/*private define*/
typedef enum MT_SINGLE_ACTION
{
    MT_ACTION_FORWORD,
    MT_ACTION_BACKWORD,
    MT_ACTION_STOP
}MTSingleAct_enum;

#define MOTOR_NUM 2
#define MOTOR_INDEX_L  0
#define MOTOR_INDEX_R  1   // must be < MOTOR_NUM

typedef struct MOTOR_PIN
{
    uint8_t DriverA;
    uint8_t DriverB;
    uint8_t Enable;  //it is unusable for no enable function chip, eg:LM1836
}MotorPin_stru;

/*    */
class BiMotor
{
private:


    MotorPin_stru MotorPin[MOTOR_NUM];
    MTSpeed_enum SpeedVal;
    uint32_t RunCnt;   //to control the distance or angle

    MTMovDir_enum LastMoveDirection;  //only base direction: MT_FORWARD,MT_BACKWARD,MT_CLOCKWISE,MT_ANTICLOCK,MT_STOP
    uint8_t LastMovePara;

    bool StepRepeatState;
    bool RotateRepeatState;
    bool RotatePingPangState;


    inline void Run();
    inline void Stop();
    inline void SetSpeed( MTSpeed_enum Speed );

    inline void Walk( MTMovDir_enum Direction, uint8_t Distance = 1 );
    inline void Rotate( MTMovDir_enum Direction, uint8_t Angle = 9 );
    void Statistic( MTMovDir_enum Direction, uint8_t Para );

    void SetSingleMotorAction( uint8_t Index, MTSingleAct_enum Action );

protected:


public:
    BiMotor();
    void Move( MTMovDir_enum Direction, uint8_t Para, MTSpeed_enum Speed = MT_SPEED_NORMAL );

    bool isMoving();
    bool isStepRepeat();
    bool isRotateRepeat();
    bool isRotatePingPang();

    void GetMoveAciton( MTMovDir_enum &Direction, uint8_t &Para );
    void TimerProc();
};

#endif

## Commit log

2012-08-08 Initial schematics, PCBs & code from Edward
2012-08-08 Added pdf & jpg of schematic & PCB
2012-08-09 Added Summary of Kicad schematic & PCB files.txt
2012-08-09 Added simple schematic of IR shield
    [IR_Shield.sch]
2012-08-09 Added simple schematic of IR shield pdf
2012-08-09 add edward's version of routed prototype which sent for printing
    [$savepcb.brd, attiny85_board_optimized.brd, attiny85_board_optimized.dsn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]
2012-08-10 updated: Summary of Kicad schematic & PCB files.txt
2012-08-11 Added: kicad/IR Shield pinouts v0.1.txt
2012-08-11 moved all old ones to the folder trash
    [attiny85_board_optimized.brd, attiny85_board_optimized.dsn, swarmrobot.brd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]
2012-08-13 Added pdf of PCB sent to manufacturing
2012-08-19 Added pin mapping spreadsheet and updated code to match the new PCBs
    [Arduino, AtTiny, L293 and header pin mappings.ods]
2012-08-30 Beautifed code & doco, added spin & turn, reverted Spanner's non working code
    [Notes_Tips_ToDO.ino]
2012-09-11 tidyup - deleted all kicad/* except edward_version, updated readme.md & Summary of Kicad schematic & PCB files.txt
2012-09-11 hopefully now actually deleting the files
    [IR_Shield.sch, attiny85_board_optimized.brd, attiny85_board_optimized.dsn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]
2012-09-11 Moving Edwards files used to manufacture to /kicad, deleting remainder
    [$savepcb.brd, attiny85_board_optimized.brd, attiny85_board_optimized.dsn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]
2012-09-11 added Atmega & uno folders, deleted WIP PWM code (will put in branch)
    [pcbmotor.brd, pcbmotor.sch]
2012-09-12 1.Code for IR-Swarmbot at source directory. The PWM library is used, so you must install the lib. 2.SoftDesign.dia should be opened by DIA software which can be download from ubuntu software center. 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
2012-09-12 Add the IR shield for swarm robot.
    [$swarmIR.sch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]
2012-09-13 added jpg of all scehmatics & PCBs
2012-09-13 IR shield PCB and notes for the new mainboard
    [$swarmIR.brd]
2012-09-15 added Pricing spreadsheet
    [Xinchejian SwarmRobot Pricing.xls]
2012-09-18 updating most Tadobao link styles due to expiry
    [Xinchejian SwarmRobot Pricing.xls]
2012-10-12 added pullups, filter cap & series R
    [swarmIR.brd, swarmIR.dsn, swarmIR.sch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]
2012-10-12 added 2 more IR Rx & pullups
    [swarmIR.brd, swarmIR.sch]
2012-10-13 routed board & updated pin map spreadsheet
    [Arduino, AtTiny, L293 and header pin mappings.ods, swarmIR.brd, swarmIR.dsn]
2012-10-13 Added 2xIR receivers, 6xpullups, filter capacitor, series R, header breakout pads
    [$swarmIR.brd, $swarmIR.sch]
2012-10-13 Some local changes
    [$swarmIR.sch, swarmIR.sch]
2012-10-17 Update the IR shield design.
    [$.brd, swarmIR.brd, swarmIR.sch]
2012-10-18 fixed unconencted pin on R6 in schematic
    [Arduino, AtTiny, L293 and header pin mappings.ods, swarmIR.sch]
2012-10-22 Move all AtTiny hardware & software directories from root to /AtTiny2313
    [$.brd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]
2012-10-22 ... now removing the old directories from repo root
    [$.brd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]
2012-10-25 Added Group control via switches to SwarmIRControl & SwarmIRControlArduino
2012-10-26 AtTiny2313/MotorTest - so it is easy wire BOTH motors up corectly
2012-10-26 Added code comments 4/8MHz fuses, updated IR shield graphics
    [swarmIR.brd, swarmIR.sch]
2012-11-01 minor group 0 bug fix
    [SwarmIRControllerArduino.ino, main.c]
2012-11-08 Add PCB design file.
    [SwBotMain.brd, SwBotMain.sch, Swbot_shield.brd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]
2012-11-08 Change UNO to ATMEGA168. Add hardware to it.
    [SwBotMain.brd, SwBotMain.sch, Swbot_shield.brd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]
2013-01-06 X-Bot V2.1 alpha
    [SwBotMain.brd, SwBotMain.sch, Swbot_shield.brd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]

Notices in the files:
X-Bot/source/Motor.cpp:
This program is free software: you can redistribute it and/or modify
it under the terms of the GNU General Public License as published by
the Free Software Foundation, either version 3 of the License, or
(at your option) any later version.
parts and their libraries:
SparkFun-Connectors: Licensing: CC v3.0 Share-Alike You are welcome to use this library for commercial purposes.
